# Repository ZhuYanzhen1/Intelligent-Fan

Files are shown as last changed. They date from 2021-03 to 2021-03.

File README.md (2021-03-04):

# Intelligent-Fan

## Catalog

+ [1. Breif Introduction](#1-breif-introduction)
+ [2. Develop Environments](#2-develop-environments)
+ [3. Control Ideas](#3-control-ideas)
+ [4. Function Design](#4-function-design)
+ [5. Bill Of Materials](#5-bill-of-materials)

***

### 1. Breif Introduction

&nbsp;&nbsp;&nbsp;&nbsp;This repository realizes the function of an intelligent fan. The repository contains the rack model file, esp8266 networking code, STM32 code and bill of materials needed for the production of this product. The main functions of this product are remote network control and automatic temperature control.

***

### 2. Develop Environments

+ Operating System: Ubuntu 20.04LTS
+ Coding IDE: CLion 2020.2.4
+ Compilation Tool Chain: gcc-none-eabi 9-2020-q2; xtensa-lx106-elf
+ Debugger: ST-Link; UART Debug Software

***

### 3. Control Ideas

&nbsp;&nbsp;&nbsp;&nbsp;The main chip is stm32f103c8t6, the WiFi chip uses esp8266ex, the temperature sampling chip uses DS18B20, and the display screen uses 1.8-inch TFT LCD screen to realize the networking time synchronization function. The matrix keyboard is used

&nbsp;&nbsp;&nbsp;&nbsp;The output PWM wave of stm32f103c8t6 is used to control the MOS tube to control the fan speed and the heating temperature of the heating wire, and the timing parameters set by the user are adjusted by reading the matrix keyboard through the IO port. Esp8266ex connects WiFi through 802.11n protocol, and realizes mqtt protocol through TCP protocol in LwIP stack. Esp8266ex connects to the server through WiFi, and mqtt subscribes to the topic of fan switch. Once the user sends the topic of the fan switch remotely, esp8266ex realizes the remote control of the fan through the high-speed STM32 serial protocol.

***

### 4. Function Design

1. Manual control (through keyboard setting, LCD screen display status, display time and fan gear)

	+ Cold air: set the wind speed through the button.

	+ Timing: power off automatically after setting a certain time by button.

	+ Hot air: set whether the heating wire works through the button.

2. Temperature control gear (display real-time temperature through LCD screen)

	+ When the temperature is less than 23 ℃, the electric fan will not rotate

	+ When 23 ≤ temperature ≤ 28 ℃, the fan rotates at low speed

	+ When the temperature is higher than 28, the fan will rotate at high speed

3. Automatic transmission

	Check whether there is someone in front of the fan, if there is someone, continue to rotate, if there is no one, count down for 15s, if there is still no one, turn off the fan.

4. Remote control of fan switch through WiFi networking

***

### 5. Bill Of Materials

| Name | Quantity | Purchase Link | Total Price |
| :---: | :---: | :---: | :---: |
|  Circuit Board  | 5 | [Purchase Link](https://www.jlc.com/#) | 5.0￥ |
| 716 Motor | 1 | [Purchase Link](https://item.taobao.com/item.htm?spm=a230r.1.14.53.45b8694ac5VVeM&id=585798412136&ns=1&abbucket=13#detail) | 2.0￥ |
| Paddle | 1 | [Purchase Link](https://item.taobao.com/item.htm?spm=a230r.1.14.53.45b8694ac5VVeM&id=585798412136&ns=1&abbucket=13#detail) | 0.8￥ |
|  STM32F103C8T6  | 1 | [Purchase Link](https://item.taobao.com/item.htm?spm=a1z10.3-c-s.w4002-21223910208.10.1ef96a4bap6D9d&id=522577960040) | 41.0￥ |
| ESP12-F | 1 | [Purchase Link](https://item.taobao.com/item.htm?spm=a1z10.3-c-s.w4002-21223910208.10.65e36a4bstI0G6&id=594418112880) | 8.0￥ |
| 1.8inch TFT-LCD | 1 | [Purchase Link](https://item.taobao.com/item.htm?spm=a1z09.2.0.0.38a82e8dd7Ke6Z&id=602381046383&_u=23ika512ceb7) | 13.5￥ |
| DS18B20 | 1 | [Purchase Link](https://item.taobao.com/item.htm?spm=a1z10.3-c-s.w4002-21223910208.13.75ef6a4bVSZETi&id=522575988442) | 5.1￥ |
|  Heating Wire | 1 | [Purchase Link](https://item.taobao.com/item.htm?id=616146535211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) | 2.6￥ |
|  AC/DC Adaptor  | 1 | [Purchase Link](https://item.taobao.com/item.htm?spm=a230r.1.14.49.509a1a8bVCJNCW&id=564383076984&ns=1&abbucket=13#detail) | 22.0￥ |

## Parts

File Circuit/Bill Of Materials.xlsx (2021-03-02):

Comment | Designator | Quantity | value
Capacitor | C1, C2 | 2 | 18pF
Capacitor | C3 | 1 | 10uF
Capacitor | C4, C5, C6, C7, C8, C9, C10, C14, C15, C16, C17, C18 | 12 | 100nF
Capacitor | C11 | 1 | 100pF
Capacitor | C12 | 1 | 10nF
Capacitor | C13 | 1 | 22uF
Diode | D1 | 1 | M7
POWER | DC_005 | 1
C-CM | EC1, EC2 | 2 | 1000uF
Key | ERST, K1, K2, K3, K4, K5, RST | 7
Inductance | L1 | 1 | 6.8uH
TFTLCD | LCD | 1 | 1.8inch
LED | LED1, LED2 | 2 | Blue
Header 2 | P1, P2, P5, P6 | 4
Header 3 | P3 | 1
Header 4 | P4 | 1
MOSFET | Q1 | 1 | IRFR3607
MOSFET | Q2, Q3 | 2 | SI2302
Resistor | R1, R3, R4, R5 | 4 | 1K
Resistor | R2, R6, R7, R8, R11, R12, R16, R17, R18, R19, R20 | 11 | 10K
Resistor | R9 | 1 | 2.1K
Resistor | R10, R13 | 2 | 100K
Resistor | R14 | 1 | 47K
Resistor | R15 | 1 | 17.6K
IC | U1 | 1 | STM32F103C8T6
IC | U2 | 1 | ESP12
IC | U3, U4, U5, U6 | 4 | AMS1117-3.3
IC | U7 | 1 | SY8303AIC
Crystal | X1 | 1 | 8M

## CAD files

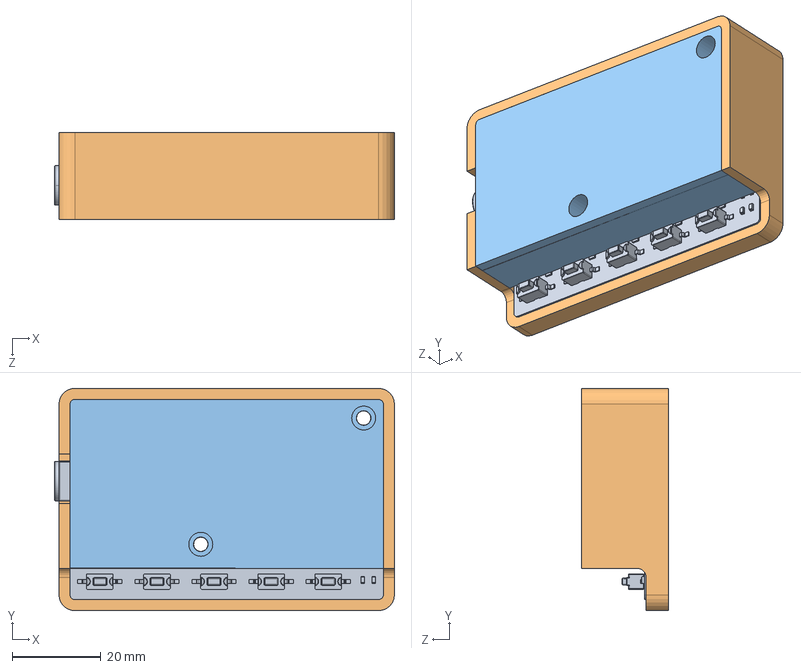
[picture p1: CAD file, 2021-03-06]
Frame/Assembly.SLDASM
76.6 x 50.1 x 19.5 mm
ControlBoard
Lower_Shell
Upperer_Shell

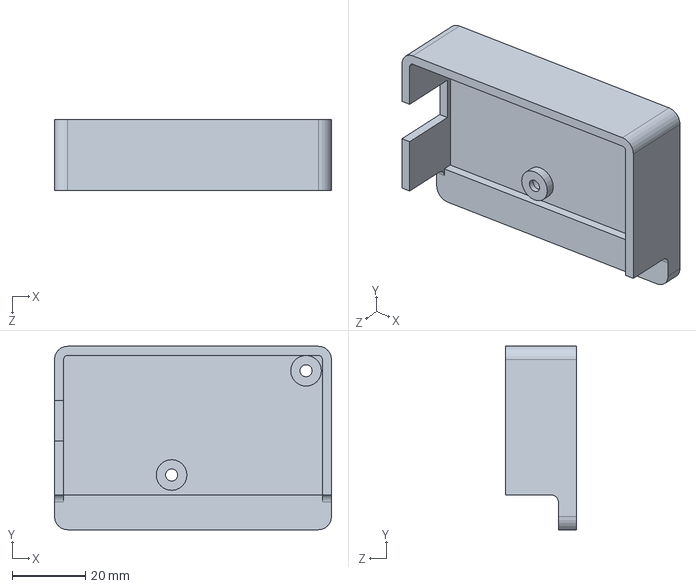
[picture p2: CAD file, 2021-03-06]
Frame/lower_Shell.SLDPRT
75.6 x 50.1 x 19.5 mm

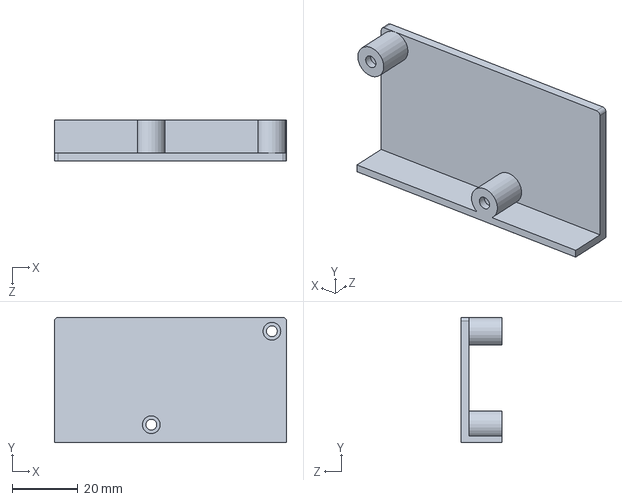
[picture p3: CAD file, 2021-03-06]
Frame/Upperer_Shell.SLDPRT
70.6 x 38.1 x 12.5 mm

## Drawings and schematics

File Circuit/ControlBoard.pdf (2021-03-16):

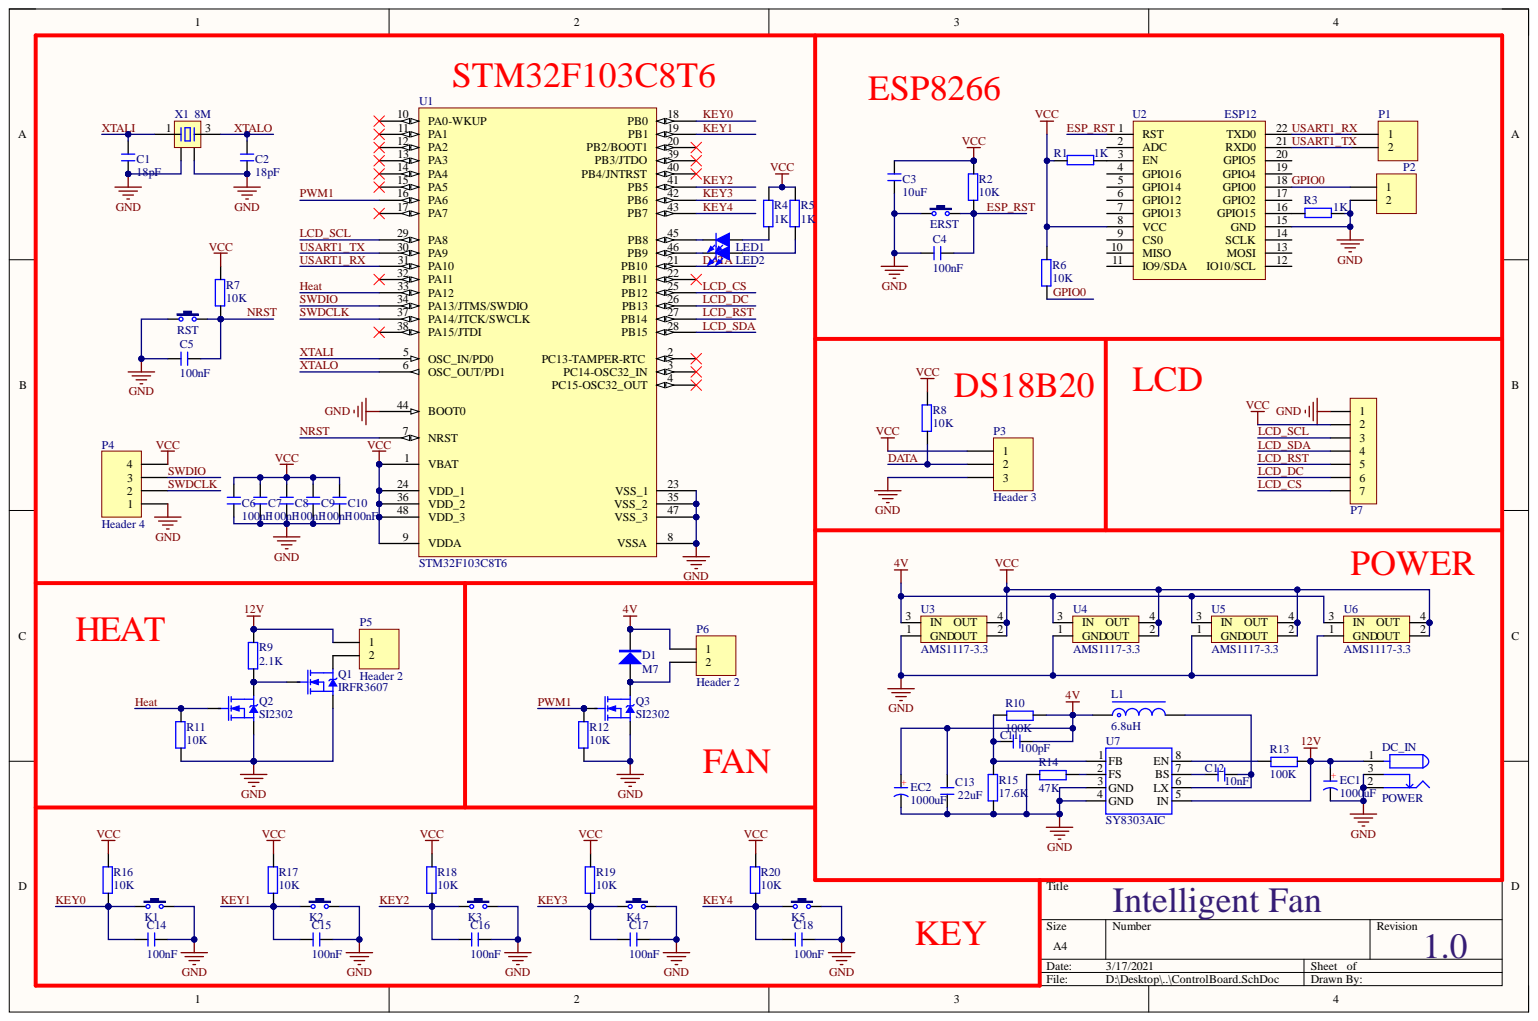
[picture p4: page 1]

GND 3 | | EC1 | 2

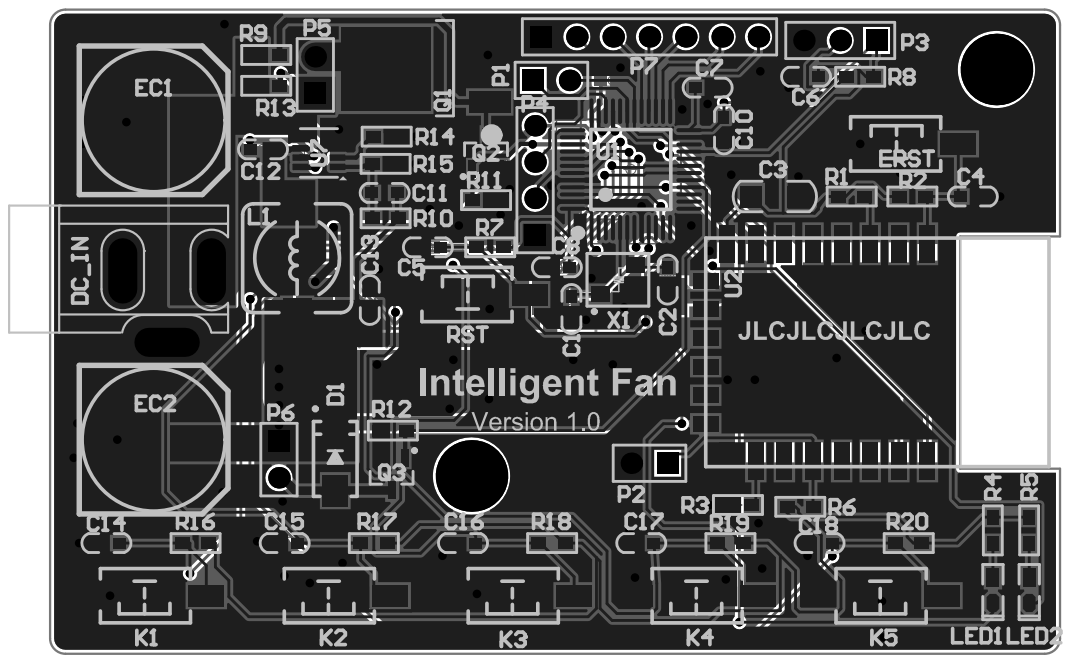
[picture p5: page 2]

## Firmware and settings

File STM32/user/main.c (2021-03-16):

#include "main.h"

Menu_Struct_t Menu;
TaskHandle_t InitTask_Handler, MenuSwitchTask_Handler;
TaskHandle_t CircleTask_Handler, MenuGUITask_Handler;

void Menu_Config(void) {
    const char buf[] = "00:00:00";
    memset(&Menu, 0x00, sizeof(Menu_Struct_t));
    Menu.Timer.Enable = DISABLE;
    Menu.Heater_Enable = DISABLE;
    Menu.Index = 1;
    Menu.SubIndex = 1;
    Menu.Body_Detect = 0;
    strcpy((char *) Menu.Time_Buf, buf);
}

void InitTask(void *pvParameters) {
    taskENTER_CRITICAL();
    GPIO_Config();
    LED_Config();
    DS18B20_Config();
    TIM3_Config();
    Fan_Off();
    UART1_Config();
    Semaphore_Config();
    LCD_Config();
    LCD_Scan(4);
    GUI_Clear(C_WHITE);
    Menu_Config();
    xTaskCreate(MenuSwitchTask, "MenuSwitchTask", 1024,
                NULL, 2, &MenuSwitchTask_Handler);
    xTaskCreate(MenuGUITask, "MenuGUITask", 512,
                NULL, 1, &MenuGUITask_Handler);
    xTaskCreate(CircleTask, "CircleTask", 512,
                NULL, 1, &CircleTask_Handler);
    vTaskDelete(NULL);
    taskEXIT_CRITICAL();
}

int main(void) {
    HAL_Config();
    Clock_Config();
    Delay_Config();
    xTaskCreate(InitTask, "InitTask", 256,
                NULL, 1, &InitTask_Handler);
    vTaskStartScheduler();
    while (1);
}

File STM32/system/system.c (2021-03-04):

//
// Created by Lao·Zhu on 2021/3/3.
//

#include "system.h"
#include "FreeRTOS.h"
#include "task.h"

TIM_HandleTypeDef htim4;
static unsigned int Facus = 0;
static unsigned int Facms = 0;

void Delayus(unsigned int xus) {
    unsigned int Ticks, Time_Old, Time_Now, Time_Count = 0;
    unsigned int Reload = SysTick->LOAD;
    Ticks = xus * Facus;
    Time_Old = SysTick->VAL;
    while (1) {
        Time_Now = SysTick->VAL;
        if (Time_Now != Time_Old) {
            if (Time_Now < Time_Old)
                Time_Count += Time_Old - Time_Now;
            else
                Time_Count += Reload - Time_Now + Time_Old;
            Time_Old = Time_Now;
            if (Time_Count >= Ticks)
                break;
        }
    }
}

void Delayms(unsigned int xms) {
    if (xTaskGetSchedulerState() == taskSCHEDULER_RUNNING) {
        if (xms >= Facms)
            vTaskDelay(xms / Facms);
        else {
            xms %= Facms;
            Delayus(xms * 1000);
        }
    } else
        Delayus(xms * 1000);
}

void Delay_Config(void) {
    unsigned int Reload;
    Facus = HAL_RCC_GetSysClockFreq() / 1000000;
    Reload = HAL_RCC_GetSysClockFreq() / 1000000;
    Reload *= 1000000 / configTICK_RATE_HZ;
    Facms = 1000 / configTICK_RATE_HZ;
    SysTick->CTRL |= SysTick_CTRL_TICKINT_Msk;
    SysTick->LOAD = Reload;
    SysTick->CTRL |= SysTick_CTRL_ENABLE_Msk;
}

void Clock_Config(void) {
    RCC_OscInitTypeDef RCC_OscInitStruct = {0};
    RCC_ClkInitTypeDef RCC_ClkInitStruct = {0};
    RCC_OscInitStruct.OscillatorType = RCC_OSCILLATORTYPE_HSE;
    RCC_OscInitStruct.HSEState = RCC_HSE_ON;
    RCC_OscInitStruct.HSEPredivValue = RCC_HSE_PREDIV_DIV1;
    RCC_OscInitStruct.HSIState = RCC_HSI_ON;
    RCC_OscInitStruct.PLL.PLLState = RCC_PLL_ON;
    RCC_OscInitStruct.PLL.PLLSource = RCC_PLLSOURCE_HSE;
    RCC_OscInitStruct.PLL.PLLMUL = RCC_PLL_MUL9;
    while (HAL_RCC_OscConfig(&RCC_OscInitStruct) != HAL_OK);
    RCC_ClkInitStruct.ClockType = RCC_CLOCKTYPE_HCLK | RCC_CLOCKTYPE_SYSCLK
        | RCC_CLOCKTYPE_PCLK1 | RCC_CLOCKTYPE_PCLK2;
    RCC_ClkInitStruct.SYSCLKSource = RCC_SYSCLKSOURCE_PLLCLK;
    RCC_ClkInitStruct.AHBCLKDivider = RCC_SYSCLK_DIV1;
    RCC_ClkInitStruct.APB1CLKDivider = RCC_HCLK_DIV2;
    RCC_ClkInitStruct.APB2CLKDivider = RCC_HCLK_DIV1;
    while (HAL_RCC_ClockConfig(&RCC_ClkInitStruct, FLASH_LATENCY_2) != HAL_OK);
    HAL_RCC_EnableCSS();
}

void HAL_MspInit(void) {
    __HAL_RCC_AFIO_CLK_ENABLE();
    __HAL_RCC_PWR_CLK_ENABLE();
    __HAL_AFIO_REMAP_SWJ_NOJTAG();
}

void HAL_TIM_PeriodElapsedCallback(TIM_HandleTypeDef *htim) {
    if (htim->Instance == TIM4)
        HAL_IncTick();
}

HAL_StatusTypeDef HAL_InitTick(uint32_t TickPriority) {
    RCC_ClkInitTypeDef clkconfig;
    uint32_t uwTimclock = 0;
    uint32_t uwPrescalerValue = 0;
    uint32_t pFLatency;
    HAL_NVIC_SetPriority(TIM4_IRQn, TickPriority, 0);
    HAL_NVIC_EnableIRQ(TIM4_IRQn);
    __HAL_RCC_TIM4_CLK_ENABLE();
    HAL_RCC_GetClockConfig(&clkconfig, &pFLatency);
    uwTimclock = 2 * HAL_RCC_GetPCLK1Freq();
    uwPrescalerValue = (uint32_t) ((uwTimclock / 1000000U) - 1U);
    htim4.Instance = TIM4;
    htim4.Init.Period = (1000000U / 1000U) - 1U;
    htim4.Init.Prescaler = uwPrescalerValue;
    htim4.Init.ClockDivision = 0;
    htim4.Init.CounterMode = TIM_COUNTERMODE_UP;
    if (HAL_TIM_Base_Init(&htim4) == HAL_OK)
        return HAL_TIM_Base_Start_IT(&htim4);
    return HAL_ERROR;
}

void HAL_SuspendTick(void) {
    __HAL_TIM_DISABLE_IT(&htim4, TIM_IT_UPDATE);
}

void HAL_ResumeTick(void) {
    __HAL_TIM_ENABLE_IT(&htim4, TIM_IT_UPDATE);
}

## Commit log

2021-03-02 Complete README and initialize circuit files
    [ControlBoard.SchDoc, PCB_Project.PrjPcb]
2021-03-02 Complete STM32F103C8 minimum system circuit design
    [ControlBoard.SchDoc, PCB_Project.PrjPcb, PcbLib1.PcbLib]
2021-03-02 Generate STM32 codes and clean temporary files of circuit
2021-03-02 Add gitignore for circuit files
2021-03-02 Complete periph circuit design
    [ControlBoard.SchDoc]
2021-03-02 Add comment for schematic diagram
    [ControlBoard.SchDoc]
2021-03-02 Complete all schematic diagram design
    [Bill Of Materials.xlsx, ControlBoard.SchDoc, PcbLib1.PcbLib]
2021-03-02 Generate PCB documents for circuit
    [ControlBoard.PcbDoc]
2021-03-02 Add keep out layer for PCB
    [ControlBoard.PcbDoc, ControlBoard.SchDoc, PcbLib1.PcbLib]
2021-03-02 Add gitignore rules for circuit
2021-03-02 Add fillet to PCB keep out layer
    [ControlBoard.PcbDoc]
2021-03-02 Complete design board frame shape
    [ControlBoard.PcbDoc]
2021-03-02 finished route
    [ControlBoard.PcbDoc, ControlBoard.SchDoc]
2021-03-02 finished all net routing
    [ControlBoard.PcbDoc, ControlBoard.SchDoc]
2021-03-02 finished all PCB design
    [ControlBoard.PcbDoc]
2021-03-02 Export gerber files
    [ControlBoard.GBL, ControlBoard.GBO, ControlBoard.GBP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]
2021-03-03 Configure cmake file and debug file for stm32
    [board.cfg]
2021-03-03 Rearrange STM32 code files
2021-03-03 add gpio initialize for stm32
2021-03-03 add lcd hardware driver codes
2021-03-03 add gui driver codes
2021-03-04 modify timer pwm output codes, enable pwm output
2021-03-05 add step modules for pcb circuit and export pcb 3d module. create lower shell module but it is reversed.
    [ControlBoard.PcbDoc, ControlBoard.PcbLib, PCB_Project.PrjPcb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]
2021-03-06 Create UART receive callback function and store command into buffer.
2021-03-06 Create fan control codes and link uart callback function to it.
2021-03-06 Create isolated LED task codes in new file.
2021-03-06 Create circle task for renew temperature and lcd display contents.
2021-03-06 Finished lower shell of frame and create assemble file.Upper shell hasn't finished yet
    [Assembly.SLDASM, Upperer_Shell.SLDPRT, lower_Shell.SLDPRT]
2021-03-09 Repair GPIOB clock disable bug.
    [gpio.c, usertask.c]
2021-03-09 Add read key function and find bug: you cannot use vsprintf to print float number, if you do that, the program will stuck in _exit() syscall function.
    [main.c, usertask.c]
2021-03-10 Change UART baudrate to make sure it is mached to esp8266 baudrate. esp8266 communicate success.
2021-03-11 Repair LCD wrong pin number bug, LCD can display now.
    [gpio.c, lcd.c, lcd.h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]
2021-03-14 Motor can adjust speed now. duty cycle must not greater than 50.
2021-03-14 Finished menu design, but it cannot clear LCD when you switching mode.
2021-03-14 Add clear LCD code when switching mode
2021-03-14 Change remote control function to avoid mode collapse
    [usart.c]
2021-03-14 Repair all menu bugs, it now can be used
    [usertask.c]
2021-03-16 Add temperature control mode
2021-03-16 Renew circuit pdf file
2021-03-16 Repair timer enable display bug
